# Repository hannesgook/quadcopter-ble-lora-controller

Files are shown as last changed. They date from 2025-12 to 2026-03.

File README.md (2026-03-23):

> ⚠️ **This project has been replaced.** See [PidraQRL](https://github.com/hannesgook/PidraQRL) for the current version, rebuilt on ESP32 with a live SAC RL agent, new comms stack, Unity digital twin, and more.

# Drone Control System

This repository contains all code developed for our Swedish upper-secondary _Gymnasiearbete_ project.  
The system implements a complete communication chain for controlling a quadcopter using BLE, LoRa, and an onboard custom Arduino-based flight controller implemented from first principles.

The entire system is built from scratch without relying on existing flight control frameworks. Standard libraries were used where appropriate, and in one case modified at the source level to meet real-time control requirements.

:medal_sports: **Qualified for the national final of Unga Forskare - Sweden's national science competition for young researchers**

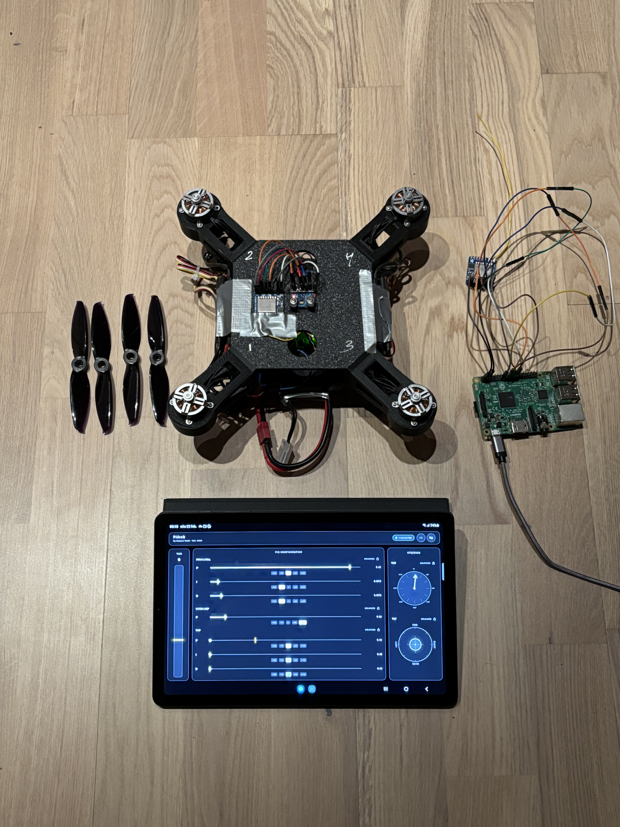
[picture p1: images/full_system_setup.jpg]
Full system setup


## Contributions

### Project Lead

**Hannes Göök**

Responsible for the overall system architecture and primary implementation, including:

- Design and implementation of the custom **Arduino-based flight controller**:
  - Cascaded angle-rate PID control logic and stabilization behavior
  - IMU data handling and orientation filtering using a Madgwick filter
  - ESC communication and motor control
  - Communication failsafe handling

- Design and implementation of the end-to-end **wireless communication chain**
  - BLE communication between the mobile app and Raspberry Pi
  - LoRa-based long-range link between Raspberry Pi and flight controller

- Development of the **Flutter-based mobile control application**
- CAD design of the quadcopter airframe (designed in Fusion 360)
- System integration and most hardware assembly

### Contributors

- **Isak Roos** – budgeting, hardware sketching and implementation, soldering, documentation, testing, and validation
- **Olle Einvall** – quadcopter sketching, documentation, security considerations, exploration, investments, and testing
- **Hugo Persson** – hardware preparation, video documentation, and testing

## Repository Structure

```
arduino_rx_drone_control/
  flight_controller/          Flight controller
  tools/                      Calibration and test utilities
    imu_deadzone_tester/      IMU deadzone measurement
    motor_assigner/           Motor order verification

raspberry_2_arduino/          Raspberry Pi LoRa bridge

cad/                          CAD files for the quadcopter airframe
  drone_frame.stl             3D-printable airframe model
images/                       Documentation images
README.md                     Project overview
LICENSE                       Project license
```

## System Overview

### 1. Mobile App to Raspberry Pi

A Flutter app that sends joystick values, throttle, and PID parameters over BLE.
BLE is used only for short-range communication between the mobile app and the Raspberry Pi.

Mobile app repo: [PidraQ](https://github.com/hannesgook/pidraq)

### 2. Raspberry Pi to Arduino

The Raspberry Pi receives BLE packets, bridges them through LoRa, and transmits them to the Arduino flight controller.
LoRa is used here to get reliable long-range control without relying on Wi-Fi or BLE.

### 3. Arduino Flight Controller

The Arduino (ATmega328P in our case) receives LoRa packets, parses control inputs, reads IMU data (MPU6050), runs a Madgwick filter, computes PID corrections, and drives four ESCs for quadcopter stabilization.

### Failsafe Behavior

The flight controller implements a communication failsafe based on LoRa packet reception.

If no valid packet is received for **1000 ms**, failsafe is triggered:

- All ESCs are immediately set to **1000 µs**
- PID computations are skipped
- Motors remain at minimum throttle until communication resumes

The failsafe state is automatically cleared as soon as a new valid LoRa packet is received.

Failsafe triggers **~1000 ms** after pressing **Disconnect** in the app, since no further LoRa packets are received.

Additional internal safety checks are implemented in the flight controller to prevent invalid motor output under certain sensor fault conditions.

### Control Notes

Setting throttle to zero does not always fully stop all motors if PID gains are not set to zero.
Stabilization corrections can still introduce motor output at low throttle.

To guarantee full motor cutoff, the communication failsafe must be triggered or the system must be disarmed.

## Quadcopter Prototype

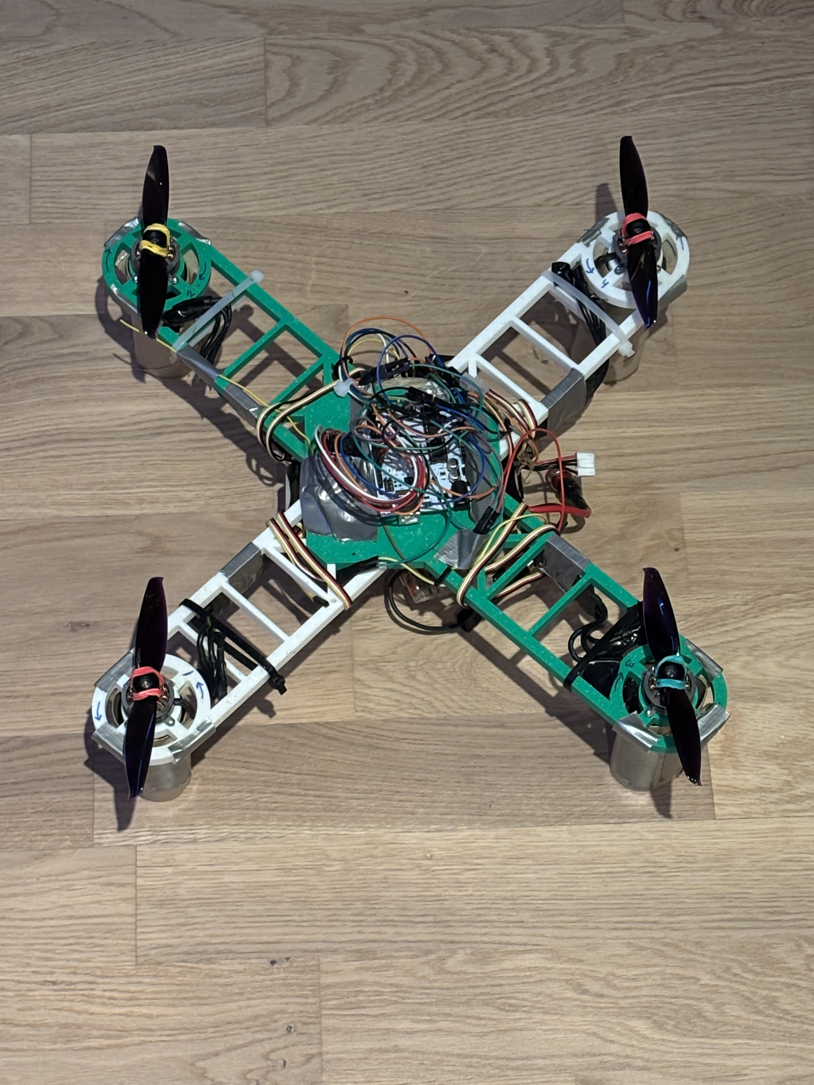
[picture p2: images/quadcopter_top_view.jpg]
Quadcopter top view


## Airframe CAD Model

The quadcopter airframe was custom-designed in Fusion 360 and is included in this repository as a single STL file:

- `cad/drone_frame.stl`
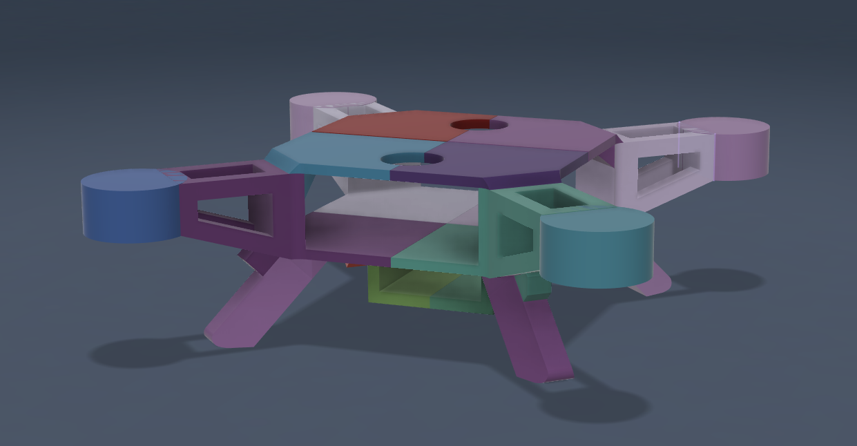
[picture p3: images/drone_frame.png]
Quadcopter CAD design
  

It represents the physical prototype used for testing.

## Status

The system has been tested on a real quadcopter built together with my project partners, and is able to take off and fly under manual control from the mobile app.

Milestones achieved:
- 5 second flight with a clean, controlled landing
- 10 second flight with a rough but planar landing

Due to limited mechanical tuning, no GPS, and non-final PID parameters, the quadcopter is not perfectly stable during takeoff and tends to drift. The controller is intended as a working prototype rather than a production-grade flight controller.

## Dependencies and Notes

This project depends on the RadioHead library, which is installed separately in Arduino IDE and is not included in this repo.
During development, I made local modifications to RadioHead.

Local changes made:

- The file `RH_ASK.cpp` was disabled (renamed to `RH_ASK.cpp.disabled`) to avoid conflicts with the LoRa module.
- Atomic sections (`ATOMIC_BLOCK_START` / `ATOMIC_BLOCK_END`) were removed in `RHSPIDriver.cpp` to prevent blocking behavior that interfered with motor timing.

These changes were required to ensure stable real-time motor control. Without them, motor timing was unreliable.

### Mobile App Notes

The mobile app has its own repository: [PidraQ](https://github.com/hannesgook/pidraq)

### Possible Next Steps

- Add a barometer module to estimate altitude and enable basic altitude hold.
- Integrate GPS to compensate for horizontal drift.

## License

This project is licensed under the MIT License.
See the `LICENSE` file for details.

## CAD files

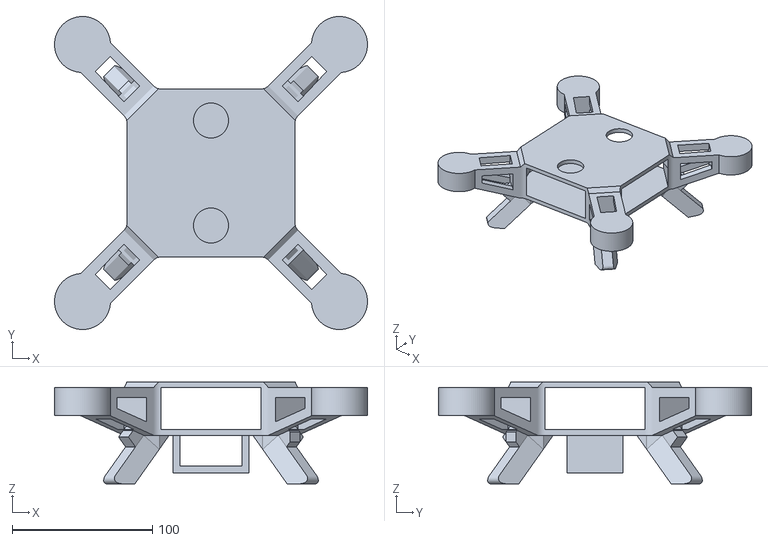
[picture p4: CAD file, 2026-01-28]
cad/drone_frame.stl
223.5 x 223.5 x 72.7

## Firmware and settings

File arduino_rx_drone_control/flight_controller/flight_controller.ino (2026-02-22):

// © 2025 Hannes Göök
// Licensed under the MIT License

#include <Servo.h>
#include <SPI.h>
#include <RH_RF95.h>
#include <Wire.h>
#include <MadgwickAHRS.h>

Servo esc1;  // D3 - Back left (spins counter-clockwise)
Servo esc2;  // D5 - Front left (spins clockwise)
Servo esc3;  // D9 - Back right (spins clockwise)
Servo esc4;  // D10 - Front right (spins counter-clockwise)

#define MPU6050_ADDR 0x68

#if defined(__AVR_ATmega32U4__)
#define RFM95_CS 8
#define RFM95_INT 7
#define RFM95_RST 4
#elif defined(ADAFRUIT_FEATHER_M0) || defined(ADAFRUIT_FEATHER_M0_EXPRESS) || defined(ARDUINO_SAMD_FEATHER_M0)
#define RFM95_CS 8
#define RFM95_INT 3
#define RFM95_RST 4
#elif defined(ARDUINO_ADAFRUIT_FEATHER_RP2040_RFM)
#define RFM95_CS 16
#define RFM95_INT 21
#define RFM95_RST 17
#elif defined(__AVR_ATmega328P__)
#define RFM95_CS 4
#define RFM95_INT 2
#define RFM95_RST 6
#elif defined(ESP8266)
#define RFM95_CS 2
#define RFM95_INT 15
#define RFM95_RST 16
#elif defined(ARDUINO_ADAFRUIT_FEATHER_ESP32S2) || defined(ARDUINO_NRF52840_FEATHER) || defined(ARDUINO_NRF52840_FEATHER_SENSE)
#define RFM95_CS 10
#define RFM95_INT 9
#define RFM95_RST 11
#elif defined(ESP32)
#define RFM95_CS 33
#define RFM95_INT 27
#define RFM95_RST 13
#elif defined(ARDUINO_NRF52832_FEATHER)
#define RFM95_CS 11
#define RFM95_INT 31
#define RFM95_RST 7
#endif

#define RF95_FREQ 433.0

class MyRF95 : public RH_RF95 {
public:
  MyRF95(uint8_t slaveSelectPin, uint8_t interruptPin = RH_INVALID_PIN, RHGenericSPI& spi = hardware_spi)
    : RH_RF95(slaveSelectPin, interruptPin, spi) {}

  void poll() { handleInterrupt(); }
};

MyRF95 rf95(RFM95_CS, RH_INVALID_PIN);
Madgwick filter;

float rollDeg = 0.0f;
float pitchDeg = 0.0f;
float yawDeg = 0.0f;

float gyroBiasX = 0.0f;
float gyroBiasY = 0.0f;
float gyroBiasZ = 0.0f;

float gx_dps = 0.0f;
float gy_dps = 0.0f;
float gz_dps = 0.0f;

float stickRoll = 0.0f;
float stickPitch = 0.0f;
float stickYaw = 0.0f;
float stickThrottle = 0.0f;

int maxThrottle = 2000;

unsigned long lastLoRaMs = 0;
float lastDt = 0.004f;

static const float LOOP_HZ = 250.0f;
static const float LOOP_DT = 1.0f / LOOP_HZ;

static const float STICK_MAX_ANGLE_DEG = 15.0f;
static const float STICK_MAX_YAW_RATE_DPS = 120.0f;

// Angle loop gains (outer loop)
float angleKP = 2.0f;
static const float ANGLE_I_DEADZONE = 0.62f;  // Don't accumulate I-term for errors below this constant
float rollAngleITerm = 0.0f;
float pitchAngleITerm = 0.0f;
float angleKI = 0.0f;

static const unsigned long FAILSAFE_CUTOFF_MS = 1000;
static const int IDLE_CUTOFF_US = 1050;

float rollArmRef = 0.0f;
float pitchArmRef = 0.0f;
bool armed = false;

bool imuHealthy = true;
unsigned long lastImuOkMs = 0;

static const float ACC_MIN_G = 0.5f;
static const float ACC_MAX_G = 1.8f;
static const unsigned long IMU_FAIL_TIMEOUT_MS = 100;

static const float STICK_MAX_YAW_ANGLE_DEG = 180.0f;   // stickYaw -1..1 maps to -180..180 deg target heading
static const float YAW_ANGLE_KP = 4.0f;                // outer yaw angle -> target yaw rate
static const float YAW_ANGLE_I_DEADZONE = 1.0f;        // deg
float yawAngleITerm = 0.0f;

float yawArmRef = 0.0f;


float constrainf(float x, float a, float b) {
  if (x < a) return a;
  if (x > b) return b;
  return x;
}

int clampUs(int us) {
  if (us < 1000) return 1000;
  if (us > maxThrottle) return maxThrottle;
  return us;
}

int throttleFromY(float y) {
  y = constrainf(y, 0.0f, 1.0f);
  if (y < 0.05f) return 1000;
  int us = 1000 + (int)(y * (maxThrottle - 1000));
  if (us > maxThrottle) us = maxThrottle;
  return us;
}

float wrapAngleDeg(float a) {
  while (a > 180.0f) a -= 360.0f;
  while (a < -180.0f) a += 360.0f;
  return a;
}

typedef struct PID {
  float kp;
  float ki;
  float kd;
  float iTerm;
  float lastRate;
  float outMin;
  float outMax;
} PID_t;

float pidRate(PID_t &pid, float targetRateDps, float measuredRateDps, float dt);
float pidRate(PID_t &pid, float targetRateDps, float measuredRateDps, float dt) {
  float error = targetRateDps - measuredRateDps;

  if (pid.ki > 0.0001f) {
    pid.iTerm += pid.ki * error * dt;
    if (pid.iTerm > pid.outMax) pid.iTerm = pid.outMax;
    if (pid.iTerm < pid.outMin) pid.iTerm = pid.outMin;
  }

  float dTerm = 0.0f;
  if (pid.kd > 0.0001f && dt > 0.0f) {
    dTerm = -pid.kd * (measuredRateDps - pid.lastRate) / dt;
  }

  pid.lastRate = measuredRateDps;

  float out = pid.kp * error + pid.iTerm + dTerm;
  if (out > pid.outMax) out = pid.outMax;
  if (out < pid.outMin) out = pid.outMin;

  return out;
}

void pidReset(PID_t &pid);
void pidReset(PID_t &pid) {
  pid.iTerm = 0.0f;
  pid.lastRate = 0.0f;
}

// Rate PIDs (inner loop)
PID_t rollRatePID  = { 0.075f, 0.0f, 0.0f, 0.0f, 0.0f, -250.0f, 250.0f };
PID_t pitchRatePID = { 0.075f, 0.0f, 0.0f, 0.0f, 0.0f, -250.0f, 250.0f };
PID_t yawRatePID   = { 10.0f, 0.5f, 0.0f, 0.0f, 0.0f, -250.0f, 250.0f };

void mpuWrite(uint8_t reg, uint8_t val) {
  Wire.beginTransmission(MPU6050_ADDR);
  Wire.write(reg);
  Wire.write(val);
  Wire.endTransmission(true);
}

void mpuInit() {
  mpuWrite(0x6B, 0x00);
  delay(100);
  mpuWrite(0x1A, 0x03);
  mpuWrite(0x19, 0x03);
  mpuWrite(0x1B, 0x00);
  mpuWrite(0x1C, 0x00);
  delay(100);
}

bool mpuReadRaw(int16_t &ax, int16_t &ay, int16_t &az,
                int16_t &gx, int16_t &gy, int16_t &gz) {
  Wire.beginTransmission(MPU6050_ADDR);
  Wire.write(0x3B);
  if (Wire.endTransmission(false) != 0) return false;

  int bytes = Wire.requestFrom(MPU6050_ADDR, 14, true);
  if (bytes != 14) return false;

  ax = (Wire.read() << 8) | Wire.read();
  ay = (Wire.read() << 8) | Wire.read();
  az = (Wire.read() << 8) | Wire.read();
  Wire.read();
  Wire.read();
  gx = (Wire.read() << 8) | Wire.read();
  gy = (Wire.read() << 8) | Wire.read();
  gz = (Wire.read() << 8) | Wire.read();

  return true;
}

void mpuCalibrateGyro() {
  const int samples = 2000;
  long sumX = 0, sumY = 0, sumZ = 0;

  for (int i = 0; i < samples; i++) {
    int16_t ax, ay, az, gx, gy, gz;
    mpuReadRaw(ax, ay, az, gx, gy, gz);
    sumX += gx;
    sumY += gy;
    sumZ += gz;
    delay(1);
  }

  gyroBiasX = (float)sumX / samples;
  gyroBiasY = (float)sumY / samples;
  gyroBiasZ = (float)sumZ / samples;
}

void updateIMU() {
  int16_t axr, ayr, azr, gxr, gyr, gzr;

  if (!mpuReadRaw(axr, ayr, azr, gxr, gyr, gzr)) {
    return;
  }

  float ax = axr / 16384.0f;
  float ay = ayr / 16384.0f;
  float az = azr / 16384.0f;

  float accMag = sqrtf(ax * ax + ay * ay + az * az);

  if (!isfinite(accMag) || accMag < 0.1f) return;


  float gxRaw = (gxr - gyroBiasX) / 131.0f;
  float gyRaw = (gyr - gyroBiasY) / 131.0f;
  float gzRaw = (gzr - gyroBiasZ) / 131.0f;

  static bool first = true;
  static float gx_f, gy_f, gz_f;

  if (first) {
    gx_f = gxRaw;
    gy_f = gyRaw;
    gz_f = gzRaw;
    first = false;
  }

  const float alphaGyro = 0.30f;
  gx_f += alphaGyro * (gxRaw - gx_f);
  gy_f += alphaGyro * (gyRaw - gy_f);
  gz_f += alphaGyro * (gzRaw - gz_f);

  gx_dps = -gx_f;
  gy_dps = gy_f;
  gz_dps = gz_f;

  filter.updateIMU(gx_f, gy_f, gz_f, ax, ay, az);

  rollDeg  = -filter.getRoll();
  pitchDeg =  filter.getPitch();
  yawDeg   = -filter.getYaw();

  if (!isfinite(rollDeg) || !isfinite(pitchDeg) || !isfinite(yawDeg)) {
    return;
  }

  imuHealthy = true;
  lastImuOkMs = millis();
}

void writeMotors(int fl, int fr, int bl, int br) {
  int cFl = clampUs(fl);
  int cFr = clampUs(fr);
  int cBl = clampUs(bl);
  int cBr = clampUs(br);

  esc2.writeMicroseconds(cFl);
  esc4.writeMicroseconds(cFr);
  esc1.writeMicroseconds(cBl);
  esc3.writeMicroseconds(cBr);
}

void stopMotorsAndReset() {
  writeMotors(1000, 1000, 1000, 1000);
  pidReset(rollRatePID);
  pidReset(pitchRatePID);
  pidReset(yawRatePID);
  rollAngleITerm = 0.0f;
  pitchAngleITerm = 0.0f;
  yawAngleITerm = 0.0f;
}


uint8_t buf[64];

static inline float u8_to_01(uint8_t b) {
  return (float)b * (1.0f / 255.0f);
}

// Matches Flutter _map11 approx. Tiny quantization error is normal.
static inline float u8_to_m11(uint8_t b) {
  return ((float)b * (1.0f / 127.5f)) - 1.0f;
}

static inline float read_f32_le(const uint8_t* p) {
  union { uint8_t b[4]; float f; } u;
  u.b[0] = p[0];
  u.b[1] = p[1];
  u.b[2] = p[2];
  u.b[3] = p[3];
  return u.f;
}

void handleLoRa() {
  rf95.poll();
  uint8_t len = sizeof(buf);

  if (!rf95.available()) return;
  if (!rf95.recv(buf, &len)) return;
  if (len < 1) return;

  const uint8_t type = buf[0];

  if (type != 'S') return;
  if (len < 33) return;
  
  stickThrottle = u8_to_01(buf[1]);
  stickRoll     = u8_to_m11(buf[2]);
  stickPitch    = u8_to_m11(buf[3]);
  stickYaw      = u8_to_m11(buf[4]);

  stickThrottle = constrainf(stickThrottle, 0.0f, 1.0f);
  stickRoll     = constrainf(stickRoll, -1.0f, 1.0f);
  stickPitch    = constrainf(stickPitch, -1.0f, 1.0f);
  stickYaw      = constrainf(stickYaw, -1.0f, 1.0f);

  const float p   = read_f32_le(buf + 5);
  const float i   = read_f32_le(buf + 9);
  const float d   = read_f32_le(buf + 13);

  const float p2  = read_f32_le(buf + 17);
  const float i2  = read_f32_le(buf + 21);
  const float d2  = read_f32_le(buf + 25);

  const float angleKP_recv = read_f32_le(buf + 29);

  rollRatePID.kp  = p;
  rollRatePID.ki  = 0.0f;
  rollRatePID.kd  = d;

  pitchRatePID.kp = p;
  pitchRatePID.ki = 0.0f;
  pitchRatePID.kd = d;

  yawRatePID.kp   = p2;
  yawRatePID.ki   = i2;
  yawRatePID.kd   = d2;

  angleKI = i;

  angleKP = angleKP_recv;

  lastLoRaMs = millis();
}


void updateStabilization() {
  if ((millis() - lastImuOkMs) > IMU_FAIL_TIMEOUT_MS) {
    imuHealthy = false;
  }

  if (!imuHealthy) {
    armed = false;
    stopMotorsAndReset();
    return;
  }

  unsigned long nowMs = millis();
  bool failsafe = (nowMs - lastLoRaMs) > FAILSAFE_CUTOFF_MS;

  int throttleUs = throttleFromY(stickThrottle);

  if ((nowMs - lastLoRaMs) > FAILSAFE_CUTOFF_MS) {
    armed = false;
    stopMotorsAndReset();
    return;
  }

  if (!armed) {
    if (throttleUs < IDLE_CUTOFF_US) {
      rollArmRef = rollDeg;
      pitchArmRef = pitchDeg;
      yawArmRef = yawDeg;
      armed = true;
    } else {
      stopMotorsAndReset();
      return;
    }
  }


  float targetRollDeg  = stickRoll  * STICK_MAX_ANGLE_DEG;
  float targetPitchDeg = -stickPitch * STICK_MAX_ANGLE_DEG;

  float rollErrDeg  = targetRollDeg  - (rollDeg - rollArmRef);
  float pitchErrDeg = targetPitchDeg - (pitchDeg - pitchArmRef);

  // Angle integral with deadzone
  if (angleKI > 0.0001f && throttleUs >= IDLE_CUTOFF_US) {
    float rollErrForI = (fabs(rollErrDeg) > ANGLE_I_DEADZONE) ? rollErrDeg : 0.0f;
    float pitchErrForI = (fabs(pitchErrDeg) > ANGLE_I_DEADZONE) ? pitchErrDeg : 0.0f;
    
    rollAngleITerm += angleKI * rollErrForI * lastDt;
    pitchAngleITerm += angleKI * pitchErrForI * lastDt;
    
    rollAngleITerm = constrainf(rollAngleITerm, -60.0f, 60.0f);
    pitchAngleITerm = constrainf(pitchAngleITerm, -60.0f, 60.0f);
  } else {
    rollAngleITerm = 0.0f;
    pitchAngleITerm = 0.0f;
  }

  float targetRollRateDps  = angleKP * rollErrDeg + rollAngleITerm;
  float targetPitchRateDps = angleKP * pitchErrDeg + pitchAngleITerm;
  float yawMeasDeg = wrapAngleDeg(yawDeg - yawArmRef);

  float targetYawDeg = stickYaw * 180.0f; // stick -1..1 -> -180..180 relative to arming heading

  float yawErrDeg = wrapAngleDeg(targetYawDeg - yawMeasDeg);

  static const float YAW_ANGLE_KP_LOCAL = 3.0f; // start 2-6
  float targetYawRateDps = YAW_ANGLE_KP_LOCAL * yawErrDeg;

  targetYawRateDps = constrainf(targetYawRateDps, -STICK_MAX_YAW_RATE_DPS, STICK_MAX_YAW_RATE_DPS);

  float yawOut = -pidRate(yawRatePID, targetYawRateDps, gz_dps, lastDt);
  float rollOut  = -pidRate(rollRatePID,  targetRollRateDps,  gx_dps, lastDt);
  float pitchOut = pidRate(pitchRatePID, targetPitchRateDps, gy_dps, lastDt);

  int fl = throttleUs + (int)pitchOut - (int)rollOut + (int)yawOut;
  int fr = throttleUs + (int)pitchOut + (int)rollOut - (int)yawOut;
  int bl = throttleUs - (int)pitchOut - (int)rollOut - (int)yawOut;
  int br = throttleUs - (int)pitchOut + (int)rollOut + (int)yawOut;

  writeMotors(fl, fr, bl, br);

  static unsigned long lastPrintMs = 0;
}

void setup() {
  pinMode(LED_BUILTIN, OUTPUT);
  pinMode(RFM95_RST, OUTPUT);
  digitalWrite(RFM95_RST, HIGH);

  Serial.begin(115200);
  while (!Serial) {}

  Wire.begin();
  Wire.setWireTimeout(25000, true);
  Wire.setClock(400000);

  mpuInit();
  delay(200);

  Serial.println("Calibrating gyro, keep quad still...");
  mpuCalibrateGyro();
  Serial.println("Gyro calibration done");

  filter.begin(LOOP_HZ);

  digitalWrite(RFM95_RST, LOW);
  delay(10);
  digitalWrite(RFM95_RST, HIGH);
  delay(10);

  if (!rf95.init()) {
    Serial.println("RFM95 init failed");
  } else {
    if (!rf95.setFrequency(RF95_FREQ)) {
      Serial.println("setFrequency failed");
    }
    rf95.setTxPower(23, false);
    rf95.setModeRx();
    Serial.println("RFM95 OK");
  }

  esc1.attach(3);
  esc2.attach(5);
  esc3.attach(9);
  esc4.attach(10);

  stopMotorsAndReset();
  delay(2000);

  lastLoRaMs = millis();

  for (int i = 0; i < 500; i++) {
    updateIMU();
    delay(4);
  }

  stickThrottle = 0.0f;
  stickRoll = 0.0f;
  stickPitch = 0.0f;
  stickYaw = 0.0f;

  //Serial.println("Setup finished");
}

void loop() {
  unsigned long microsLive = micros();
  static unsigned long lastImuMicros = microsLive;
  static unsigned long lastLoRaCheckMs = 0;

  unsigned long nowMicros = microsLive;
  float dt = (nowMicros - lastImuMicros) / 1000000.0f;

  if (dt >= LOOP_DT) {
    lastImuMicros = nowMicros;
    if (dt > 0.02f) dt = 0.02f;
    lastDt = dt;

    updateIMU();
    updateStabilization();
  }

  unsigned long nowMs = millis();
  if (nowMs - lastLoRaCheckMs >= 20) {
    lastLoRaCheckMs = nowMs;
    handleLoRa();
  }
}

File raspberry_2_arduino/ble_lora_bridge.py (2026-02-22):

# SPDX-FileCopyrightText: 2018 Brent Rubell for Adafruit Industries
# SPDX-License-Identifier: MIT

# Modifications and new code © 2025 Hannes Göök

# When text is received over BLE, it is transmitted over LoRa.

import time
import busio
from digitalio import DigitalInOut
import board
import adafruit_rfm9x
from bluezero import adapter, peripheral, device
import threading
import queue


# --- LoRa Setup ---
CS0 = DigitalInOut(board.CE1)
RESET0 = DigitalInOut(board.D22)
spi = busio.SPI(board.SCK, MOSI=board.MOSI, MISO=board.MISO)

rfm9x = None
try:
    rfm9x = adafruit_rfm9x.RFM9x(spi, CS0, RESET0, 433.0)
    rfm9x.tx_power = 20  # dBm
    print("RFM9x: Detected and initialized")
except RuntimeError as error:
    print("RFM9x Error:", error)

# --- BLE UART Setup ---
UART_SERVICE = '6E400001-B5A3-F393-E0A9-E50E24DCCA9E'
RX_CHARACTERISTIC = '6E400002-B5A3-F393-E0A9-E50E24DCCA9E'
TX_CHARACTERISTIC = '6E400003-B5A3-F393-E0A9-E50E24DCCA9E'

class UARTDevice:
    tx_obj = None
    connected = False

    lora_queue = queue.Queue(maxsize=1)
    lora_thread = None
    running = True

    @classmethod
    def start_lora_thread(cls):
        if cls.lora_thread is None:
            t = threading.Thread(target=cls._lora_loop, daemon=True)
            cls.lora_thread = t
            t.start()

    @classmethod
    def _enqueue_latest(cls, pkt: bytes):
        while True:
            try:
                cls.lora_queue.put_nowait(pkt)
                break
            except queue.Full:
                try:
                    cls.lora_queue.get_nowait()
                except queue.Empty:
                    break

    @classmethod
    def _lora_loop(cls):
        last_send = 0.0
        while cls.running:
            pkt = cls.lora_queue.get()
            if pkt is None:
                break

            if not cls.connected:
                print("Dropped LoRa packet, BLE disconnected")
                continue

            now = time.time()
            dt = now - last_send
            target_period = 0.1
            if dt < target_period:
                time.sleep(target_period - dt)

            if not cls.connected:
                print("Skipped LoRa send, BLE disconnected after wait")
                continue

            if not rfm9x:
                print("RFM9x not initialized")
                continue

            try:
                rfm9x.send(pkt)  # <-- raw bytes
                last_send = time.time()
                # print("Sent over LoRa:", pkt.hex())
            except Exception as e:
                print("LoRa send failed:", e)

    @classmethod
    def flush_queue(cls):
        try:
            with cls.lora_queue.mutex:
                cls.lora_queue.queue.clear()
        except Exception:
            pass

    @classmethod
    def on_connect(cls, ble_device: device.Device):
        cls.connected = True
        print("Connected to", ble_device.address)

    @classmethod
    def on_disconnect(cls, adapter_address, device_address):
        cls.connected = False
        cls.tx_obj = None
        cls.flush_queue()
        print("Disconnected from", device_address)

    @classmethod
    def uart_notify(cls, notifying, characteristic):
        if notifying:
            cls.tx_obj = characteristic
        else:
            cls.tx_obj = None

    @classmethod
    def update_tx(cls, value):
        if cls.tx_obj and cls.connected:
            cls.tx_obj.set_value(value)

    @classmethod
    def uart_write(cls, value, options):
        if not cls.connected:
            print("Ignoring RX, no BLE device connected")
            return

        raw = bytes(value)        # <-- raw bytes from BLE
        # print("BLE RX:", raw.hex())

        cls._enqueue_latest(raw)
        cls.update_tx(value)      # echo back if you want

def main(adapter_address):
    UARTDevice.start_lora_thread()

    ble_uart = peripheral.Peripheral(adapter_address, local_name='BLE-LoRa-Bridge')

    ble_uart.add_service(srv_id=1, uuid=UART_SERVICE, primary=True)

    # RX characteristic (BLE to Pi) NOT USED
    ble_uart.add_characteristic(
        srv_id=1, chr_id=1, uuid=RX_CHARACTERISTIC,
        value=[], notifying=False,
        flags=['write', 'write-without-response'],
        write_callback=UARTDevice.uart_write,
        read_callback=None,
        notify_callback=None
    )

    # TX characteristic (Pi to BLE)
    ble_uart.add_characteristic(
        srv_id=1, chr_id=2, uuid=TX_CHARACTERISTIC,
        value=[], notifying=False,
        flags=['notify'],
        notify_callback=UARTDevice.uart_notify,
        read_callback=None,
        write_callback=None
    )

    ble_uart.on_connect = UARTDevice.on_connect
    ble_uart.on_disconnect = UARTDevice.on_disconnect

    print("Starting BLE UART peripheral...")
    ble_uart.publish()


if __name__ == '__main__':
    try:
        main(list(adapter.Adapter.available())[0].address)
    finally:
        UARTDevice.running = False
        UARTDevice.lora_queue.put(None)

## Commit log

2025-12-05 Remove jitter
2026-01-06 Document failsafe, decrease LoRa RX buffer, add yaw PID control via app
2026-01-12 Arduino code cleanup
2026-01-12 Correct pitch and yaw signs
2026-01-25 Update drone model, roll & pitch signs, and documentation
2026-01-28 Flight controller rework (cascaded PID), repo restructuring
    [flight_controller.ino, imu_deadzone_tester.ino, motor_assigner.ino]
2026-01-28 Invert joystick pitch
2026-01-28 Add airframe STL model and CAD images
    [drone_frame.stl]
2026-02-22 Move mobile app to separate repo, switch to binary comms, update README and images
